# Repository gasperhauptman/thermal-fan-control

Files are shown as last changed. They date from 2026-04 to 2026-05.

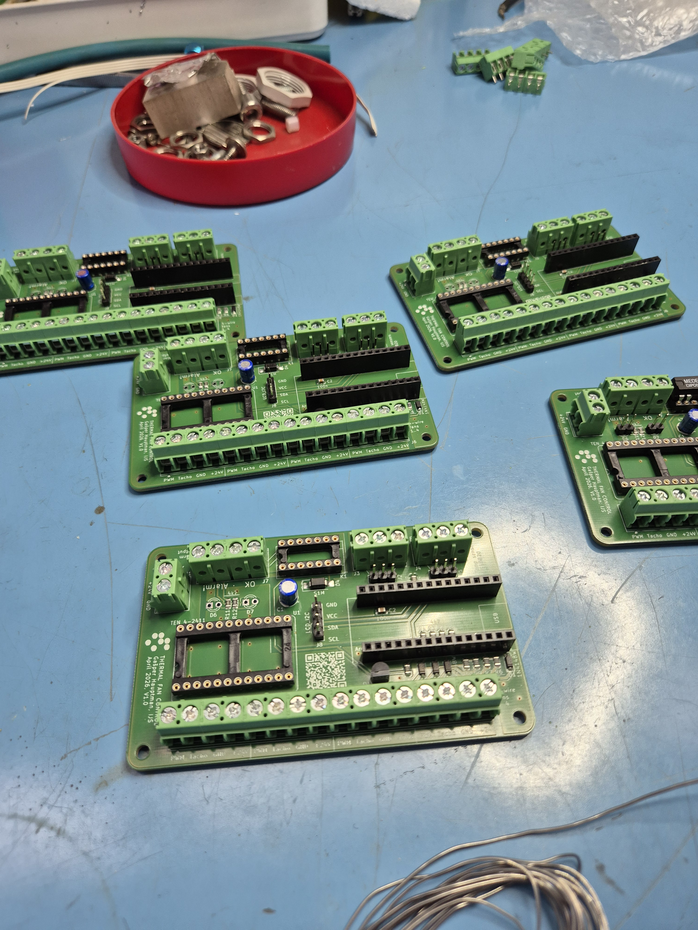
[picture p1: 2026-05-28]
v1.0/photos/20260526_111546.jpg

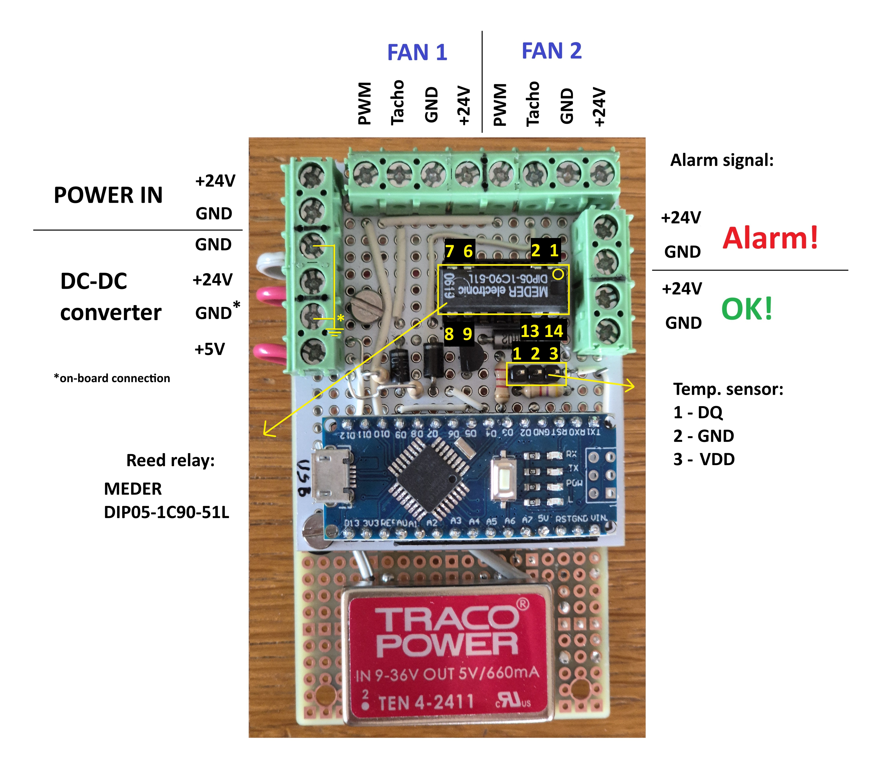
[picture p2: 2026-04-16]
prototype/pin labels.jpg

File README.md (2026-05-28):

# Thermal Fan Controller

A 4-channel PWM fan controller based on Arduino Nano, designed for active thermal management with reduced noise levels and electrical consumption in mind. Built for the Institut Jožef Stefan (Ljubljana, 2026), as part of a University of Ljubljana, Faculty of Electrical Engineering (UL FE) internship project.

## Features

- Controls up to 4 PWM fans across 2 independent channels
- Support for 1 or 2 DS18B20 temperature sensors
- Linear duty cycle curve between two temperature limits
- RPM monitoring via tacho signal for each fan
- Alarm output on high temperature or low fan RPM
- 16x2 I2C LCD display with real-time status
- Serial monitor output for debugging and sensor setup
- Watchdog timer for automatic recovery from lockups
- Fully configurable via `#define` parameters at the top of the Arduino sketch

## Hardware

- Arduino Nano
- Up to 2x Dallas DS18B20 temperature sensors (1-Wire interface)
- Up to 4x 4-wire DC fans
- 16x2 LCD with I2C backpack
- Custom PCB (included in repository)
- Traco Power TEN 4-2411 DC/DC converter (24V → 5V)
- Reed relay for alarm output

## Repository Structure

This repository contains two versions of the project:

- `prototype/` — initial prototype version
- `v1.0/` — first full version with custom PCB, includes all files listed below

```
/
├── prototype/
├── v1.0/
│   ├── firmware/          # Arduino sketch (.ino)
│   ├── libraries/         # All included libraries (source files)
│   │   ├── lib_I2CLCD/    # Modified I2C LCD library
│   │   ├── DallasTemperature/
│   │   └── OneWire/
│   ├── pcb/               # PCB design files
│   ├── case/              # 3D model files (.step)
│   └── photos/            # Photos of assembled board
└── README.md
```

## Wiring / Pin Assignment

| Function | Arduino Pin |
|---|---|
| Temperature bus | D2 |
| PWM channel 1 | D9 |
| PWM channel 2 | D10 |
| Alarm output | D3 |
| Fan 1 tacho | D4 |
| Fan 2 tacho | D5 |
| Fan 3 tacho | D6 |
| Fan 4 tacho | D7 |
| LCD | I2C (A4/A5) |

## Configuration

All user parameters are at the top of the sketch under `USER SET PARAMETERS`:

| Parameter | Description |
|---|---|
| `SERIAL_FREQ` | Serial baud rate, set to 0 to disable |
| `NUM_SENSORS` | Number of connected temperature sensors (1 or 2) |
| `FAN_MASK` | Bitmask of occupied fan slots, e.g. `0b0111` for fans 1–3  |
| `PWM_FREQ` | PWM frequency in Hz (typically 25000 for PC fans) |
| `UPDATE_FREQ` | Measurement interval in ms (minimum 800ms) |
| `UPPER_LIM` | Temperature at which fans run at 100% |
| `LOWER_LIM` | Temperature at which fans run at minimum duty |
| `MIN_DUTY` | Minimum duty cycle (0.0 to 1.0) |
| `ALARM_TEMP`  | Temperature threshold for alarm |
| `PULSE_COUNT` | Tacho pulses per revolution (typically 2) |
| `MIN_RPM` | Minimum RPM before alarm triggers (0 to disable) |

### Fan Mask

`FAN_MASK` is a 4-bit mask where each bit represents a fan slot:

```
0b(fan4)(fan3)(fan2)(fan1)
```

Example: `0b0111` means fans connected in slots 1, 2 and 3, while slot 4 is empty.

### Adding a New Temperature Sensor

1. Connect the sensor and open the serial monitor
2. At startup, the sketch prints the address of all detected sensors
3. Copy the address into `sensor1` or `sensor2` in the sketch

A separate `Address_reader` sketch is also included for convenience.

## LCD Display

- Spinning icon in top-left indicates the system is running
- Temperature shown in °C, `No Con.` if sensor can't be found (check if address is correct in sketch)
- Duty cycle shown as percentage or `MAX`
- Fan icons blink when RPM is below `MIN_RPM`
- `!` next to temperature when alarm threshold is exceeded

## Alarm Output

Pin D3 outputs `LOW` when any of the following occur:

- Any monitored fan RPM drops below `MIN_RPM`
- Any sensor reads above `ALARM_TEMP`
- Any sensor is disconnected

## Dependencies

All required libraries are included in the `v1.0/libraries` directory and can be installed manually into the Arduino libraries folder. Original sources:

- [DallasTemperature](https://github.com/milesburton/Arduino-Temperature-Control-Library)
- [OneWire](https://github.com/PaulStoffregen/OneWire)
- lib_I2CLCD — modified version of [Arduino-I2C-RW1063-0B-002](https://github.com/JeffVi/Arduino-I2C-RW1063-0B-002) by JeffVi

## Photos

Photos of the assembled board are in the `v1.0/photos` directory.

## License

No license specified. All rights reserved unless stated otherwise.  
Contact the author for usage permissions.

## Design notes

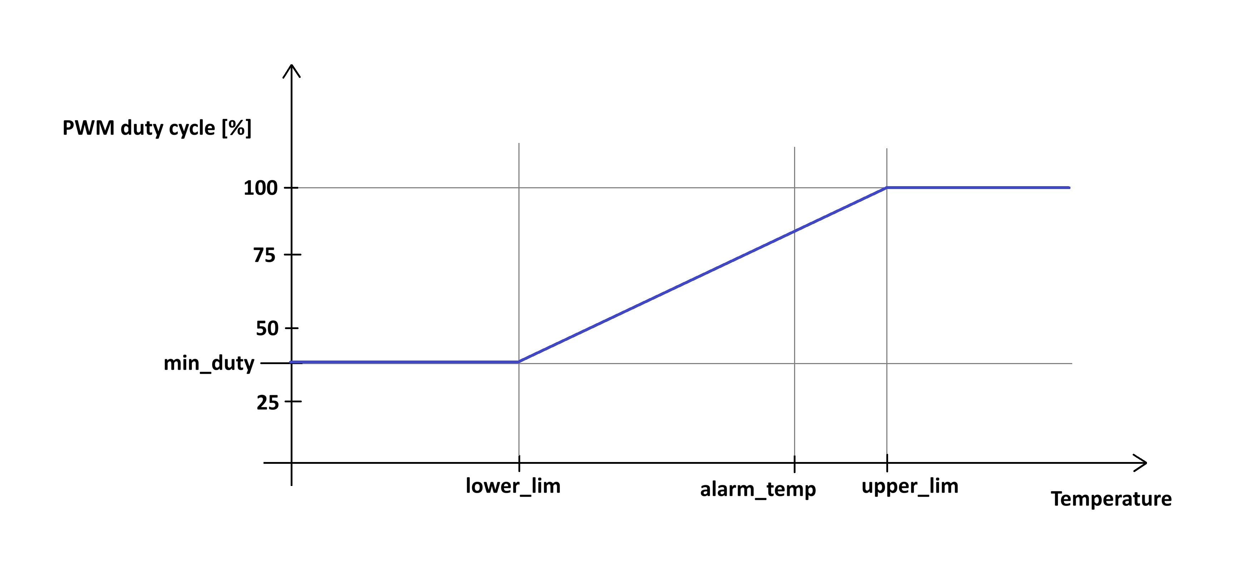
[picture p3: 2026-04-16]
prototype/graph pwm duty cycle.jpg

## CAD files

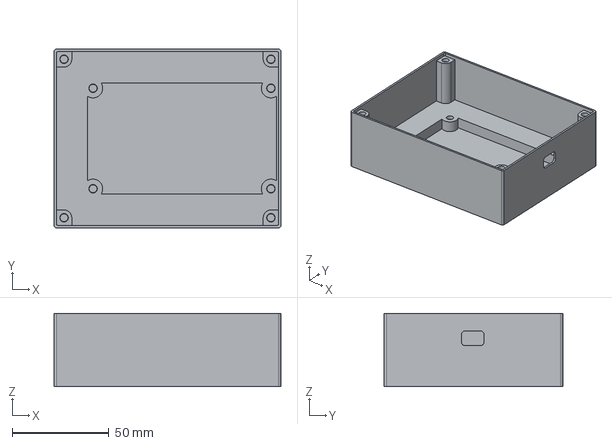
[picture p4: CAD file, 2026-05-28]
v1.0/case/bottom case.step
117.4 x 92.4 x 38.0 mm

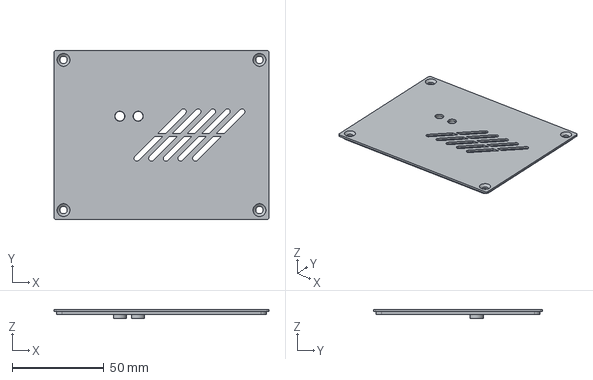
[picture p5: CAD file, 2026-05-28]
v1.0/case/lid without lcd.step
117.4 x 92.4 x 5.00 mm

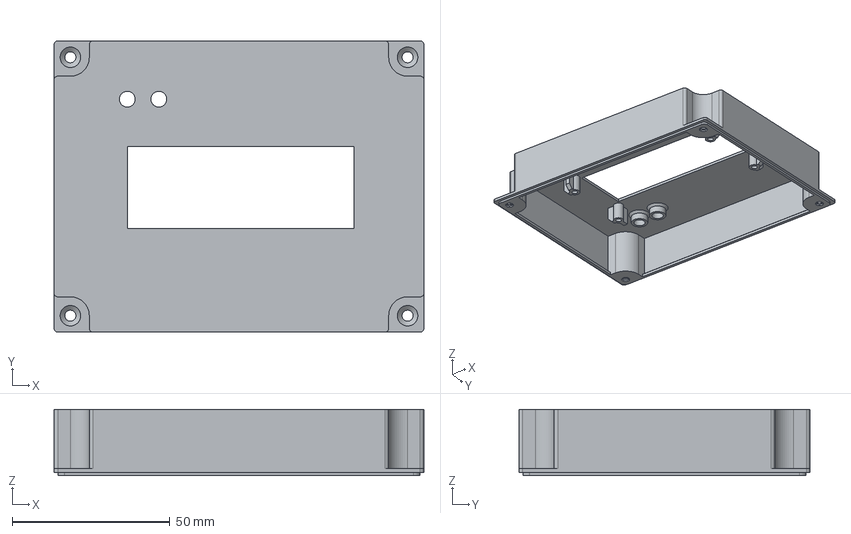
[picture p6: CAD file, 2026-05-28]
v1.0/case/lid with 16x2 lcd.step
117.4 x 92.4 x 21.0 mm

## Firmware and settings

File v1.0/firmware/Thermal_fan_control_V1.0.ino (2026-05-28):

//libraries for using Dallas temperature sensor DS18B20 and lcd
#include <OneWire.h>
#include <DallasTemperature.h>
#include "lib_I2CLCD.h"
#include <avr/wdt.h>

//********************** USER SET PARAMETERS ***********************************************************************************************************************************

#define SERIAL_FREQ 115200  //set a frequnecy that serial commnunication runs on, set to 0 to disable serial monitoring

//conected devices, fans and temperature sensors
#define NUM_SENSORS 2    // number of connected temperature sensors (1..2), when only 1 sensor is connected, all 4 fan slots (pwm outputs) are controlled by that sensor
#define FAN_MASK 0b0101  // which slots have fan connected, "0b(fan4)(fan3)(fan2)(fan1)", 1 if fan is present, 0 if slot is empty, for example 0b0111

//defines arduino pins for I/O devices (do not change when using V1.0 PCB)
#define ONEWIREBUS 2  //pin temperature sensors are connected to
#define FAN1PWM 9     //PWM1 output pin, controls fan 1 and 2
#define FAN2PWM 10    //PWM2 output pin, controls fan 3 and 4
#define ALARM 3       //pin that outputs "0" when alarm is triggered
#define FANPIN1 4     //pin that tacho from first fan is connected to
#define FANPIN2 5     //same for second fan
#define FANPIN3 6     //third
#define FANPIN4 7     //and fourth

//set a frequency of PWM required by driven fan
#define PWM_FREQ 25000  //in Hz (usually around 25kHz for PC fans)

//set a measururing/PWM refresh frequency
#define UPDATE_FREQ 1000  //period in miliseconds (limited by temperature to digital convertion speed of temperature sensors, which is ~750ms @ 12bits .. ~96ms @ 9bits)

//set diferent temperatures that define how duty cycle is calculated
#define UPPER_LIM 40   //temperature above which duty cycle is always 100%
#define LOWER_LIM 25   //temperature below which duty cycle is at it's minimum value      //between these 2 values, PWM duty cycle is linear from set MIN_DUTY value to 100%
#define MIN_DUTY 0.2   //minimum duty cycle value, set between 0 and 1 (0 and 100%)
#define ALARM_TEMP 35  //temperature at which alarm is triggered, usually same as UPPER_LIM but can be set at different value

//fan parameters
#define PULSE_COUNT 2  //set a number of pulses given by fan each rotation (usually 2 for computer fans)
#define MIN_RPM 1000    //lower limit for fan rpm, if lower than, alarm is triggered (set to 0 to disable low rpm alarm)

//when installing new sensor, you must paste sensor's addresses here, can be copied from serial monitor at start up of the system!
//if only using 1 sensor, put it's address under sensor1 !
DeviceAddress sensor1 = { 0x28, 0x92, 0xAD, 0x43, 0x51, 0x20, 0x01, 0x39 };
DeviceAddress sensor2 = { 0x28, 0xEE, 0x35, 0xB1, 0x0C, 0x00, 0x00, 0xD7 };

//***********************************************************************************************************************************************************************************

OneWire oneWire(ONEWIREBUS);
DallasTemperature T_sensor(&oneWire);

#define PWM_COUNTER ((F_CPU / PWM_FREQ) - 1)

float TempC[2];
bool alarmStatus = 0;  // 0=failure (high temp or low fan rpm), 1=OK
float duty[2] = {1.0, 1.0};  // start at full speed until first reading
bool errorTemp[2];
bool ErrorTemp = 0;
bool errorRPM[4];
bool ErrorRPM = 0;
int lcd = 0;

unsigned long lastTempUpdate = 0;
unsigned long lastDisplayUpdate = 0;
bool convRequested = 0;
unsigned long convStart = 0;

struct Fan {
  uint8_t pin;
  volatile unsigned long last;
  volatile unsigned long period;
  volatile int loopCount;
  float rpm;
};

Fan fans[4];

//definitions of custom characters for LCD
uint8_t degreeChar[8] = { 0x0E, 0x0A, 0x0E, 0x00, 0x00, 0x00, 0x00, 0x00 };
uint8_t fanChar[8] = { 0x00, 0x00, 0x19, 0x0B, 0x04, 0x1A, 0x13, 0x00 };
uint8_t breathing1[8] = { 0x08, 0x08, 0x08, 0x00, 0x00, 0x00, 0x00, 0x00 };
uint8_t breathing2[8] = { 0x04, 0x08, 0x10, 0x00, 0x00, 0x00, 0x00, 0x00 };
uint8_t breathing3[8] = { 0x00, 0x1C, 0x00, 0x00, 0x00, 0x00, 0x00, 0x00 };
uint8_t breathing4[8] = { 0x10, 0x08, 0x04, 0x00, 0x00, 0x00, 0x00, 0x00 };

//code that only runs once at every start of the system
void setup() {
  wdt_disable();
  if (SERIAL_FREQ > 0) Serial.begin(SERIAL_FREQ);
  fans[0].pin = FANPIN1;
  fans[1].pin = FANPIN2;
  fans[2].pin = FANPIN3;
  fans[3].pin = FANPIN4;
  pinMode(ALARM, OUTPUT);
  for (int i = 0; i < 4; i++) {
    pinMode(fans[i].pin, INPUT);
    fans[i].last = micros();
    fans[i].period = 0;
    fans[i].loopCount = 0;
    fans[i].rpm = 0;
  }
  PCICR |= 0b00000100;
  PCMSK2 |= 0b11110000;
  T_sensor.begin();
  sensorCheck();
  T_sensor.setResolution(12);  // 9..12
  lcdBegin();
  InitPWM();
  writePWM(duty[0], duty[1]);
  interrupts();
  wdt_enable(WDTO_4S);
}

//code running continiously after setup() is complete
void loop() {
  // temp conversion request every UPDATE_FREQ miliseconds
  if (!convRequested && millis() - lastTempUpdate >= UPDATE_FREQ) {
    requestTemp();
    convStart = millis();
    convRequested = 1;
  }
  // read temp result after 750ms and calculate all important values
  if (convRequested && millis() - convStart >= 800) {
    convRequested = 0;
    lastTempUpdate = millis();
    readTemp();
    getFanSpeed();
    writePWM(duty[0] = getDuty(TempC[0]), duty[1] = getDuty(TempC[NUM_SENSORS > 1 ? 1 : 0]));
    updateLED();
    serialData();
  }
  // display updates independently of measuring frequency
  if (millis() - lastDisplayUpdate >= 400) {
    lastDisplayUpdate = millis();
    updateLCD();
  }
  wdt_reset();
}

ISR(PCINT2_vect) {  //checks for pin changes on tacho pins, interrupt routine
  static uint8_t lastPort = 0xFF;
  uint8_t port = PIND;
  unsigned long now = micros();

  if ((lastPort & (1 << PIND4)) && !(port & (1 << PIND4))) {
    fans[0].period += (now - fans[0].last);
    fans[0].loopCount++;
    fans[0].last = now;
  }

  if ((lastPort & (1 << PIND5)) && !(port & (1 << PIND5))) {
    fans[1].period += (now - fans[1].last);
    fans[1].loopCount++;
    fans[1].last = now;
  }

  if ((lastPort & (1 << PIND6)) && !(port & (1 << PIND6))) {
    fans[2].period += (now - fans[2].last);
    fans[2].loopCount++;
    fans[2].last = now;
  }

  if ((lastPort & (1 << PIND7)) && !(port & (1 << PIND7))) {
    fans[3].period += (now - fans[3].last);
    fans[3].loopCount++;
    fans[3].last = now;
  }

  lastPort = port;
}

void requestTemp(void) {  //sends request to temp sensors to start temp to digital convertion and returns without waiting for results
  T_sensor.setWaitForConversion(0);
  T_sensor.requestTemperatures();
}

void readTemp(void) {  //reads digital value of measured temperature once convertion is finished
  TempC[0] = T_sensor.getTempC(sensor1);
#if NUM_SENSORS >= 2
  TempC[1] = T_sensor.getTempC(sensor2);
#else
  TempC[1] = -127;  // mark as not connected
#endif
}

float getDuty(float temp) {  //returns duty cycle as a result of function of measured temperature and set temperature limits
  if (temp < -100) return 1.0;
  if (temp <= LOWER_LIM) return MIN_DUTY;
  if (temp >= UPPER_LIM) return 1.0;
  return MIN_DUTY + (temp - LOWER_LIM) * (1.0 - MIN_DUTY) / (UPPER_LIM - LOWER_LIM);
}

void getFanSpeed(void) {
  noInterrupts();
  for (int i = 0; i < 4; i++) {
    if (!(FAN_MASK & (1 << i))) continue;  // skip empty slots
    fans[i].rpm = fans[i].loopCount > 0 ? (1 / (((fans[i].period / 1000000.0) / fans[i].loopCount) * PULSE_COUNT)) * 60 : 0;
    fans[i].loopCount = 0;
    fans[i].period = 0;
  }
  interrupts();
}
void writePWM(float value1, float value2)  //writes given duty cycles into timer1 compare registers
{
  value1 = constrain(value1, 0.0, 1.0);
  value2 = constrain(value2, 0.0, 1.0);
  OCR1A = (uint16_t)(value1 * ICR1);
  OCR1B = (uint16_t)(value2 * ICR1);
}

void updateLED(void) {  //update alarm status based on system state
  //check RPM
  ErrorRPM = 0;
  for (int i = 0; i < 4; i++) {
    if (!(FAN_MASK & (1 << i))) {  // slot empty
      errorRPM[i] = 0;
      continue;
    }
    if (fans[i].rpm < MIN_RPM) {
      ErrorRPM = 1;
      errorRPM[i] = 1;
    } else errorRPM[i] = 0;
  }
  //check temperatures
  ErrorTemp = 0;
  for (int i = 0; i < NUM_SENSORS; i++) {
    if (TempC[i] >= ALARM_TEMP || TempC[i] < -100) {
      ErrorTemp = 1;
      errorTemp[i] = 1;
    } else errorTemp[i] = 0;
  }
  //set or reset alarm
  if (ErrorRPM || ErrorTemp) alarmStatus = 0;
  else alarmStatus = 1;
  digitalWrite(ALARM, alarmStatus);
}

void serialData(void) {  //prints current values of fan speed, temperature and alarm status
  if (SERIAL_FREQ == 0) return;
  Serial.print("RPM: ");
  for (int i = 0; i < 4; i++) {
    Serial.print(fans[i].rpm, 0);
    if (i < 4 - 1) Serial.print(", ");
  }
  Serial.print("    Temp('C): ");
  Serial.print(TempC[0]);
#if NUM_SENSORS >= 2
  Serial.print(", ");
  Serial.print(TempC[1]);
#endif
  Serial.print("     Fan_power(%): ");
  Serial.print(duty[0] * 100);
  Serial.print(", ");
  Serial.print(duty[1] * 100);
  if (alarmStatus) Serial.println("     OK");
  else {
    Serial.print("     Alarm");
    if (ErrorTemp && ErrorRPM) Serial.println(" - high measured temperature and low fan speed!");
    else if (ErrorTemp && !ErrorRPM) Serial.println(" - high measured temperature!");
    else if (!ErrorTemp && ErrorRPM) Serial.println(" - low fan speed, check fan(s)");
    else Serial.println("");
  }
}

void sensorCheck(void) {  //checks for connected and missing temperature sensors and reports to user using serial monitor
  if (SERIAL_FREQ == 0) return;
  Serial.println("----------------------------------------------------------------------------------------------------");
  Serial.println();
  Serial.print("Devices found: ");
  Serial.println(T_sensor.getDeviceCount());
  Serial.println();
  Serial.println("Paste this addresses into code when installing a new temperature sensor:");
  DeviceAddress sensorAddr;
  for (uint8_t i = 0; i < T_sensor.getDeviceCount(); i++) {
    if (T_sensor.getAddress(sensorAddr, i)) {
      Serial.print("Connected sensor ");
      Serial.print(i + 1);
      Serial.print(" address: ");
      printAddress(sensorAddr);
    } else {
      Serial.print("Failed to read sensor at index ");
      Serial.println(i);
    }
  }
  Serial.println();
  if (!T_sensor.isConnected(sensor1)) {
    Serial.print("Sensor1 not found! - ");
    printAddress(sensor1);
  }
#if NUM_SENSORS >= 2
  if (!T_sensor.isConnected(sensor2)) {
    Serial.print("Sensor2 not found! - ");
    printAddress(sensor2);
  }
#endif
  Serial.println();
  Serial.println("----------------------------------------------------------------------------------------------------");
}

void printAddress(DeviceAddress sensorAddr) {  //prints 64-bit temperature sensor address in format, that can be directly copied into code
  if (SERIAL_FREQ == 0) return;
  for (uint8_t i = 0; i < 8; i++) {
    Serial.print("0x");
    if (sensorAddr[i] < 16) Serial.print("0");
    Serial.print(sensorAddr[i], HEX);
    if (i < 7) Serial.print(", ");
  }
  Serial.println();
}

void lcdBegin(void) {  //begins LCD communication, defines custom characters and displays device name
  Wire.begin();
  initLCD();
  clearDisplayLCD();
  cursorOFF();
  returnHomeLCD();
  printDisplayLCD("Thermal fan ctrl");
  locateCursorLCD(0, 1);
  printDisplayLCD("IJS, 2026");
  createCharLCD(0, degreeChar);
  createCharLCD(1, fanChar);
  createCharLCD(3, breathing1);
  createCharLCD(4, breathing2);
  createCharLCD(5, breathing3);
  createCharLCD(6, breathing4);
  delay(2000);
  clearDisplayLCD();
}

static int prev_lcd = -1;
static float prev_TempC[2] = { 999.0f, 999.0f };
static float prev_duty[2] = { -1.0f, -1.0f };
static bool prev_errorTemp[2] = { 0, 0 };
static bool prev_errorRPM[4] = { 1, 1, 1, 1 };  // force first draw

void updateLCD(void) {  //updates lcd based on what data changed
  lcd++;
  if (lcd > 3) lcd = 0;
  // spinning icon on row 0 only
  locateCursorLCD(0, 0);
  printCustomCharLCD(lcd + 3);
  for (int i = 0; i < 2; i++) {
    // blank col 0 on row 1 (no icon there)
    if (i == 1) {
      locateCursorLCD(0, 1);
      printDisplayLCD(" ");
    }
    // --- Temperature column ---
    bool tempChanged = (TempC[i] != prev_TempC[i]) || (errorTemp[i] != prev_errorTemp[i]) || ((lcd % 2) != (prev_lcd % 2));
    if (tempChanged) {
      locateCursorLCD(1, i);
      if (i >= NUM_SENSORS) {
        printDisplayLCD("        ");
      } else if (TempC[i] == -127) {
        printDisplayLCD("No Con. ");
      } else {
        printFloatLCD(TempC[i], 5, 1);
        printCustomCharLCD(0);
        printDisplayLCD("C");
        if (lcd % 2 && errorTemp[i]) printDisplayLCD("!");
        else printDisplayLCD(" ");
      }
      prev_TempC[i] = TempC[i];
      prev_errorTemp[i] = errorTemp[i];
    }
    // --- Duty column ---
    int dutyIdx = i < NUM_SENSORS ? i : 0;
    int dutyPct = (int)round(duty[dutyIdx] * 100);
    int prevDutyPct = (int)round(prev_duty[i] * 100);  // <-- use i, not dutyIdx
    if (dutyPct != prevDutyPct) {
      locateCursorLCD(9, i);
      if (dutyPct >= 100) printDisplayLCD(" MAX ");
      else {
        printIntLCD(dutyPct, 3);
        printDisplayLCD("% ");
      }
      prev_duty[i] = duty[dutyIdx];  // <-- store into i slot, not dutyIdx slot
    }
    // --- Fan indicators ---
    for (int a = 0; a < 2; a++) {
      int fanIdx = i * 2 + a;
      bool fanChanged = (FAN_MASK & (1 << fanIdx)) && (errorRPM[fanIdx] != prev_errorRPM[fanIdx]);
      bool blinkChanged = ((lcd < 2) != (prev_lcd < 2)) && (FAN_MASK & (1 << fanIdx)) && errorRPM[fanIdx];

      if (fanChanged || blinkChanged) {
        locateCursorLCD(14 + a, i);
        if (!(FAN_MASK & (1 << fanIdx))) printDisplayLCD(" ");
        else if (errorRPM[fanIdx] && lcd < 2) printDisplayLCD(" ");
        else printCustomCharLCD(1);
        if (FAN_MASK & (1 << fanIdx)) prev_errorRPM[fanIdx] = errorRPM[fanIdx];
      }
    }
  }
  prev_lcd = lcd;
}

void InitPWM(void) {         //set timer1 as PWM generator with outputs on pins D9 and D1
  pinMode(FAN1PWM, OUTPUT);  // D9
  pinMode(FAN2PWM, OUTPUT);  // D10
  // Stop timer
  TCCR1A = 0;
  TCCR1B = 0;
  TCNT1 = 0;
  // Fast PWM, TOP = ICR1 (Mode 14)
  TCCR1A = (1 << COM1A1) | (1 << COM1B1) | (1 << WGM11);
  TCCR1B = (1 << WGM13) | (1 << WGM12) | (1 << CS10);  // prescaler = 1
  ICR1 = PWM_COUNTER;
  OCR1A = 0;
  OCR1B = 0;
}

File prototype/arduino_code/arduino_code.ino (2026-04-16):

//libraries for using Dallas temperature sensor DS18B20
#include <OneWire.h>
#include <DallasTemperature.h>

//********************** USER SET PARAMETERS ************************************************************************************

#define serial_freq 115200  //set a frequnecy that serial commnunication runs on, set to 0 to disable serial monitoring

//defines arduino pins for I/O devices
#define OneWireBus 2  //pin temperature sensor is connected to
#define fanPWM 9      //do not modify
#define alarmLED 3    //pin that outputs logical high when alarm is triggered
#define fanPin1 4     //pin that tacho from first fan is connected to
#define fanPin2 5     //same for second fan

//set a frequency of pwm required by driven fan
#define frekvenca_pwm 25000  //in Hz

//set a measururing/PWM refresh frequency
#define updateFreq 1  //period in seconds, not including temp -> digital convertion time

//set diferent temperatures that define how duty cycle is controlled
#define upper_lim 45   //temperature above which duty cycle is always 100%
#define lower_lim 30   //temperature below which duty cycle is at it's minimum value      //between these 2 values, PWM duty cycle is linear from set min_duty value to 100%
#define min_duty 0.5   //minimum duty cycle value, between 0 and 1 (0 and 100%)
#define alarm_temp 50  //temerature at which alarm is triggered

//fan parameters
#define pulse_count 2  //set a number of pulses given by a fan per rotation
#define minSpeed 1000  //lower limit for fan rpm, if lower than, alarm is triggered

//*********************************************************************************************************************************

OneWire oneWire(OneWireBus);
DallasTemperature T_sensor(&oneWire);

float TempC = 0;
int counter = 16000000 / frekvenca_pwm - 1;
int duty = 0;
unsigned long lastUpdate = 0;
bool ledState = 0;  // 0=failure (high temp or low fan rpm), 1=OK

struct Fan {
  uint8_t pin;
  volatile unsigned long last;
  volatile unsigned long period;
  volatile int loopCount;
  float rpm;
};

Fan fans[2];

void setup() {

  if (serial_freq > 0) Serial.begin(serial_freq);

  fans[0].pin = fanPin1;
  fans[1].pin = fanPin2;

  pinMode(fanPWM, OUTPUT);
  pinMode(alarmLED, OUTPUT);

  for (int i = 0; i < 2; i++) {
    pinMode(fans[i].pin, INPUT);
    fans[i].last = micros();
    fans[i].period = 0;
    fans[i].loopCount = 0;
    fans[i].rpm = 0;
  }

  T_sensor.begin();
  if (serial_freq > 0) {
    Serial.print("Number of connected OneWire devices: ");
    Serial.println(T_sensor.getDeviceCount());
  }

  InitPWM();

  PCICR |= 0b00000100;   //enable portd interrupts
  PCMSK2 |= 0b00110000;  //enable pins d4 and d5

  interrupts();
}

void loop() {
  if (millis() - lastUpdate >= updateFreq * 1000) {
    lastUpdate = millis();
    getTemp();
    getFanSpeed();
    serialData();
    writePWM(getDuty(TempC) * counter);
    updateLED();
  }
}

ISR(PCINT2_vect) {
  static uint8_t lastPort = 0xFF;
  uint8_t port = PIND;
  unsigned long now = micros();

  // Detects falling edge on D4
  if ((lastPort & (1 << PIND4)) && !(port & (1 << PIND4))) {
    fans[0].period += (now - fans[0].last);
    fans[0].loopCount++;
    fans[0].last = now;
  }

  // Detects falling edge on D5
  if ((lastPort & (1 << PIND5)) && !(port & (1 << PIND5))) {
    fans[1].period += (now - fans[1].last);
    fans[1].loopCount++;
    fans[1].last = now;
  }
  lastPort = port;
}

void getTemp(void) {
  T_sensor.requestTemperatures();
  TempC = T_sensor.getTempCByIndex(0);
}

float getDuty(float temp) {
  if (temp <= lower_lim) return min_duty;
  if (temp >= upper_lim) return 1.0;
  return min_duty + (temp - lower_lim) * (1.0 - min_duty) / (upper_lim - lower_lim);
}

void getFanSpeed(void) {
  noInterrupts();

  for (int i = 0; i < 2; i++) {
    fans[i].rpm = fans[i].loopCount > 0 ? (1 / (((fans[i].period / 1000000.0) / fans[i].loopCount) * pulse_count)) * 60 : 0;
  }

  for (int i = 0; i < 2; i++) {
    fans[i].loopCount = 0;
    fans[i].period = 0;
  }
  interrupts();
}

void writePWM(uint16_t value) {
  if ((value >= 0) && (value < (counter + 1))) {
    OCR1A = value;
  }
}

void updateLED(void) {
  if (fans[0].rpm < minSpeed || fans[1].rpm < minSpeed) {
    ledState = 0;
  } else {
    if (TempC >= alarm_temp || TempC < -100) ledState = 0;
    else if (TempC < (alarm_temp - 1)) ledState = 1;
  }
  digitalWrite(alarmLED, ledState);
}

void serialData(void) {
  if (serial_freq > 0) {
    Serial.print("RPM_1 = ");
    Serial.print(fans[0].rpm);
    Serial.print(", RPM_2 = ");
    Serial.print(fans[1].rpm);
    Serial.print(", Temp = ");
    Serial.print(TempC);
    if (ledState) Serial.println(", OK");
    else Serial.println(", Alarm!");
  }
}
  
void InitPWM(void)  //get PWM on pin D9
{
  TCCR1B = (0 << ICNC1) | (0 << ICES1) | (0 << WGM13) | (0 << WGM12) | (0 << CS12) | (0 << CS11) | (0 << CS10); 

  TCCR1A = (1 << COM1A1) | (0 << COM1A0) | (0 << COM1B1) | (0 << COM1B0) | (1 << WGM11) | (0 << WGM10);  
  ICR1 = counter;
  TCNT1 = 0;
  OCR1B = 0;
  OCR1A = 0;
  TIMSK1 = (0 << ICIE1) | (0 << OCIE1B) | (0 << OCIE1A) | (0 << TOIE1);
  DDRB |= (1 << DDB1);
  
  TCCR1B = (0 << ICNC1) | (0 << ICES1) | (1 << WGM13) | (1 << WGM12) | (0 << CS12) | (0 << CS11) | (1 << CS10);
}

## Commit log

2026-05-28 Revise README for Thermal Fan Controller project
    Updated project description, features, hardware details, and repository structure in README.
2026-05-28 v1.0 files added
    [bottom case.step, lid with 16x2 lcd.step, lid without lcd.step]
